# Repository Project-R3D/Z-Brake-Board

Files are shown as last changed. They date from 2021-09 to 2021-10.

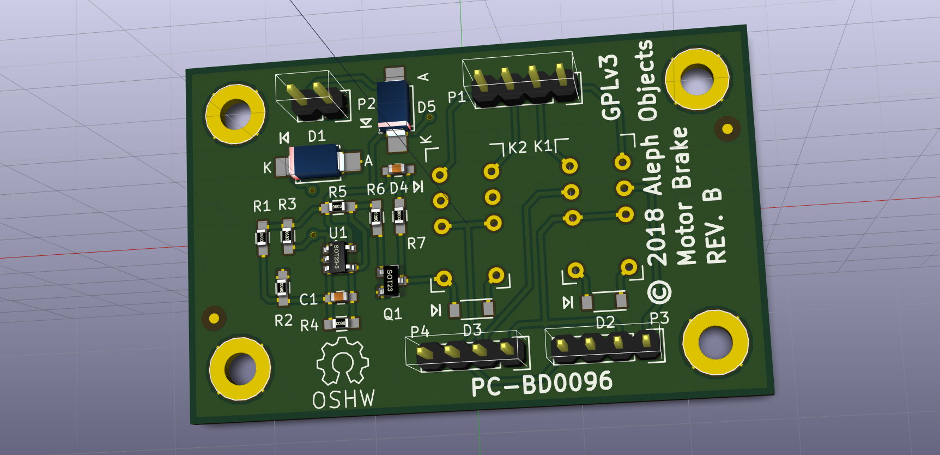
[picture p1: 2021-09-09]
Original_Lulz_Design/Z_Brake/Z_Brake.png

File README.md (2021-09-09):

# Lulzbot Z Motor Automatic Brake

The [original design files](/Original_Lulz_Design/) contained within this repository were backed up from http://devel.lulzbot.com/electronics/dolores/ on Sept 8, 2021.
In case that gets taken down as well, please see this [archive.org](https://web.archive.org/web/20200216141835/http://devel.lulzbot.com/electronics/dolores/) backup as well.

This repository acts as a backup to that original design (which was sadly removed from all other Lulzbot servers) while complying with the original `CC BY SA 4.0` AND `GPL v3` license.

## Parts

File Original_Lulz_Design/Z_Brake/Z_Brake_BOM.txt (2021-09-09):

Z_BRAKE BILL OF MATERIALS (BOM)

REFERENCE	DESCRIPTION					MFR. PART NUMBER	MFR.				NOTE

C1		Capacitor SMT 0603 Ceramic 0.22uF 50V X7R	CL10B224KB8VPNC		Samsung Electro-Mechanics
D1		Zener Diode SMA SMT 10.0V 1W +/- 5%		SMAZ10-13-F		Diodes Incorporated
D2		Schottky Diode SMT SOD-123 40V 300mA		BAT54ZFILM		STMicroelectronics
D3		Schottky Diode SMT SOD-123 40V 300mA		BAT54ZFILM		STMicroelectronics
D4		LED SMT 0603 Yellow Clear                       LTST-C190YKT		Lite-On Inc.
K1		Relay DIP 24V 2A DPDT				EC2-24NU		Kemet
K2		Relay DIP 24V 2A DPDT				EC2-24NU		Kemet
P1		Connector SL Header 4-Pin 1x4 0.100 Shrouded	0705430003		Molex, LLC
P2		Connector SL Header 2-Pin 1x2 0.100 Shrouded	0705430001		Molex, LLC
P3		Connector SL Header 4-Pin 1x4 0.100 Shrouded	0705430003		Molex, LLC
P4		Connector SL Header 4-Pin 1x4 0.100 Shrouded	0705430003		Molex, LLC
Q1		Transistor FET N-Channel SMT SOT-23 60V		2N7002			Central Semiconductor Corp	Vgs must be 30VDC minimum
R1		Resistor SMT 0603 12.4 k 1%			RC0603FR-0712K4L	Yageo
R2		Resistor SMT 0603 10.0 k 1%			RC0603FR-0710KL		Yageo
R3		Resistor SMT 0603 10.0 k 1%			RC0603FR-0710KL		Yageo
R4		Resistor SMT 0603 180 k 1%			RC0603FR-07180KL	Yageo
R5		Resistor SMT 0603 10.0 k 1%			RC0603FR-0710KL		Yageo
R6		Resistor SMT 0603 3.30 k 1%			RC0603FR-073K3L		Yageo
U1		IC SMT SOT-23-5 LM397				LM397MF/NOPB		Texas Instruments

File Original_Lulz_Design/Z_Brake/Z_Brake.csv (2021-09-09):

Id | Designator | Package | Quantity | Designation | Supplier and ref
1 | K1,K2 | EC2_Relay | 2 | EC2-24NU
2 | C1 | C_0603_HandSoldering | 1 | 0.22uF
3 | D1 | SMA_Handsoldering | 1 | 10.0 V ZENER
4 | D2,D3 | SOD-123 | 2 | D_Schottky_ALT
5 | D4 | C_0603_HandSoldering | 1 | LED_ALT
6 | Q1 | SOT-23 | 1 | 2N7002
7 | R1 | R_0603_HandSoldering | 1 | 12.6k
8 | R2,R3,R5,R6 | R_0603_HandSoldering | 4 | 10k
9 | R4 | R_0603_HandSoldering | 1 | 100k
10 | R7 | R_0603_HandSoldering | 1 | 3.3k
11 | U1 | SOT-23-5 | 1 | LM397
12 | P1,P3,P4 | Pin_Header_Straight_1x04 | 3 | CONN_01X04
13 | P2 | Pin_Header_Straight_1x02 | 1 | CONN_01X02
14 | MH1,MH2,MH3,MH4 | MOUNT_HOLE | 4 | CONN_01X01
15 | REF** | Symbol_OSHW-Logo_SilkScreen | 1 | Symbol_OSHW-Logo_SilkScreen
16 | D5 | SMA_Handsoldering | 1 | D_ALT

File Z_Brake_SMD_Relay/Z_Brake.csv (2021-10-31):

Comment | Designator | Footprint | LCSC
0.22uF | C1 | Capacitor_SMD:C_0603_1608Metric_Pad1.08x0.95mm_HandSolder
10.0 V ZENER | D1 | Diode_SMD:D_SMA_Handsoldering
D_Schottky_ALT | D2,D3 | Diode_SMD:D_SOD-123
LED | D4 | LED_SMD:LED_0603_1608Metric_Pad1.05x0.95mm_HandSolder
D_ALT | D5 | Diode_SMD:D_SMA_Handsoldering
EC2-24NU | K1,K2 | Relay_SMD:Relay_DPDT_Kemet_EE2_NU
CONN_01X01 | MH1,MH2,MH3,MH4 | MountingHole:MountingHole_2.5mm_Pad
CONN_01X04 | P1,P3 | Molex:Molex-70543-0038-0-0-MFG
CONN_01X02 | P2 | Molex:MOLEX_0705430001
2N7002 | Q1 | Package_TO_SOT_SMD:SOT-23_Handsoldering
12.4k | R1 | Resistor_SMD:R_0603_1608Metric_Pad0.98x0.95mm_HandSolder
180k | R4 | Resistor_SMD:R_0603_1608Metric_Pad0.98x0.95mm_HandSolder
10k | R2,R3,R5,R6 | Resistor_SMD:R_0603_1608Metric_Pad0.98x0.95mm_HandSolder
3.3k | R7 | Resistor_SMD:R_0603_1608Metric_Pad0.98x0.95mm_HandSolder
M2012C390 | RV1,RV2 | Resistor_SMD:R_0805_2012Metric_Pad1.20x1.40mm_HandSolder
LM397 | U1 | Package_TO_SOT_SMD:SOT-23-5_HandSoldering

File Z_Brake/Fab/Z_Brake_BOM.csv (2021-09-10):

Qty | Reference(s) | MPN | Manufacturer | Primary Supplier | Supplier PN
1 | C1 | CL10B224KB8VPNC | Samsung | Digikey | 1276-6600-1-ND
1 | D1 | SMAZ10-13-F | Diodes Incorporated | Digikey | SMAZ10-FDICT-ND
2 | D2, D3 | BAT48ZFILM | STMicroelectronics | Digikey | 497-5712-1-ND
1 | D4 | LTST-C190YKT | Lite-On Inc. | Digikey | 160-1184-1-ND
1 | D5 | CDBA340-HF | Comchip Technology | Digikey | 641-1748-1-ND
2 | K1, K2 | EC2-24NU | Kemet | Digikey | 399-11037-5-ND
2 | P1, P3 | 705430003 | Molex | Digikey | WM4802-ND
1 | P2 | 705430001 | Molex | Digikey | WM4800-ND
1 | Q1 | 2N7002 TR PBFREE | Central Semiconductor Corp | Digikey | 1514-2N7002TRPBFREECT-ND
1 | R1 | RC0603FR-0712K4L | YAGEO | Digikey | 311-12.4KHRCT-ND
4 | R2, R3, R5, R6 | RC0603FR-0710KL | YAGEO | Digikey | 311-10.0KHRCT-ND
1 | R4 | RC0603FR-07180KL | YAGEO | Digikey | 311-180KHRCT-ND
1 | R7 | RC0603FR-073K3L | YAGEO | Digikey | 311-3.30KHRCT-ND
2 | RV1, RV2 | AVR-M2012C390KT6AB | TDK | Digikey | 445-2549-1-ND
1 | U1 | LM397MF/NOPB | TI | Digikey | LM397MF/NOPBCT-ND

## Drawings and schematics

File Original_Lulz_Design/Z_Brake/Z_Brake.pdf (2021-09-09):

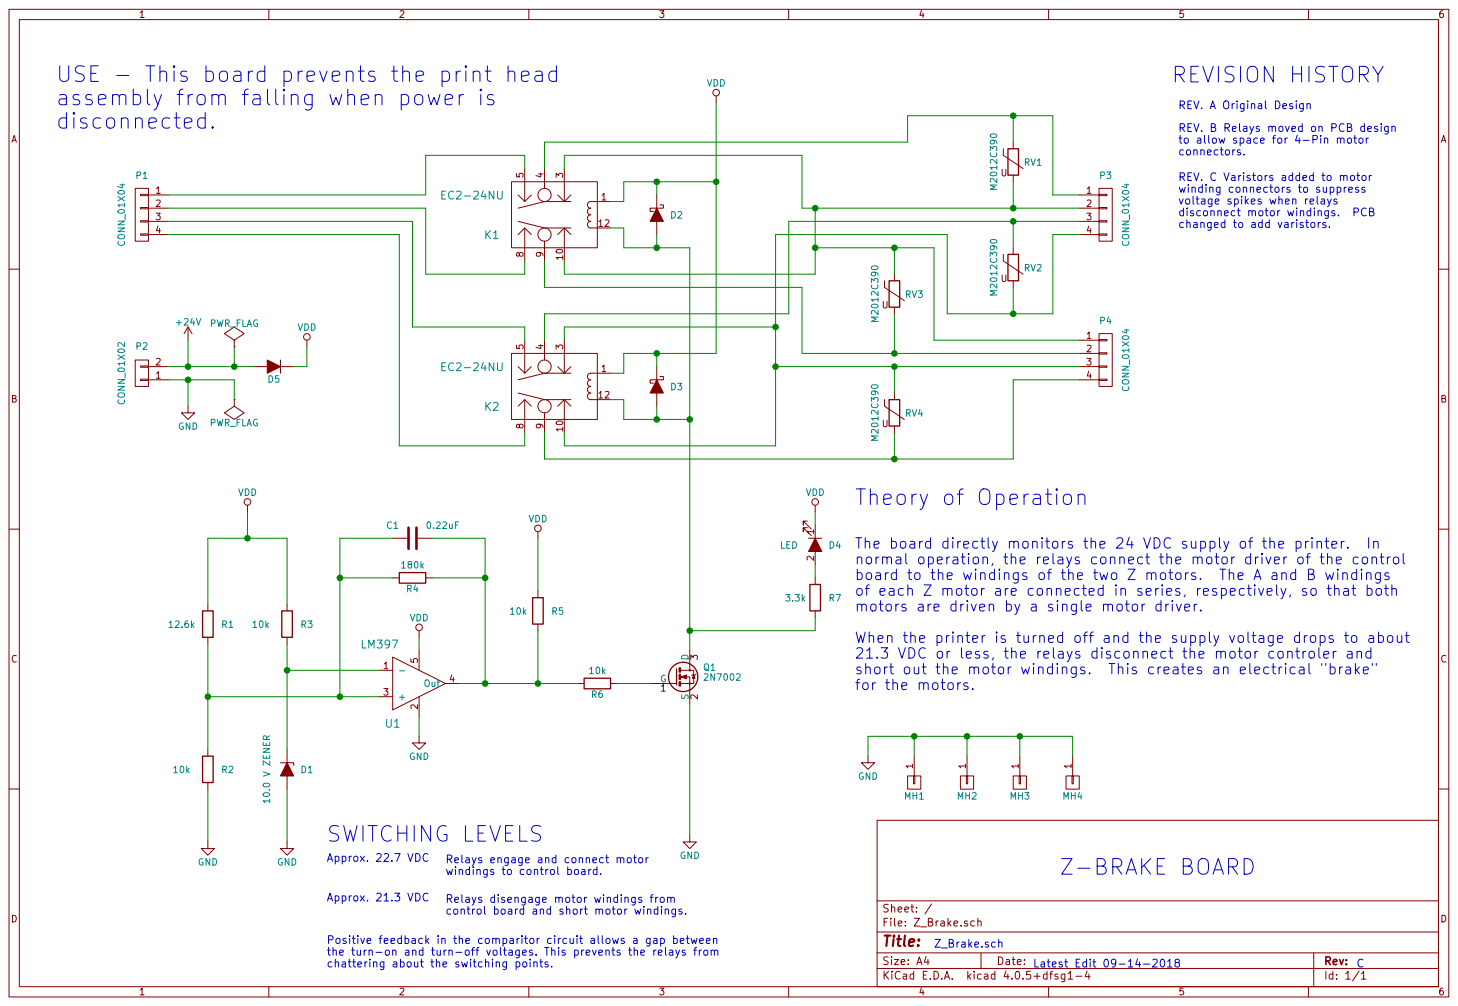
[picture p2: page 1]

USE - This board prevents the print head
assembly from falling when power is
disconnected.

REV. A Original Design
REV. B Relays moved on PCB design
to allow space for 4-Pin motor connectors. REV. C Varistors added to motor winding connectors to suppress

voltage spikes when relays
changed to add varistors.

The board directly monitors the 24 VDC supply of the printer. In
normal operation, the relays connect the motor driver of the control
board to the windings of the two Z motors. The A and B windings
of each Z motor are connected in series, respectively, so that both
motors are driven by a single motor driver.
When the printer is turned off and the supply voltage drops to about
21.3 VDC or less, the relays disconnect the motor controler and
short out the motor windings. This creates an electrical "brake"
for the motors.

Relays engage and connect motor
windings to control board.

Relays disengage motor windings from
control board and short motor windings.

Positive feedback in the comparitor circuit allows a gap between
the turn-on and turn-off voltages. This prevents the relays from
chattering about the switching points.

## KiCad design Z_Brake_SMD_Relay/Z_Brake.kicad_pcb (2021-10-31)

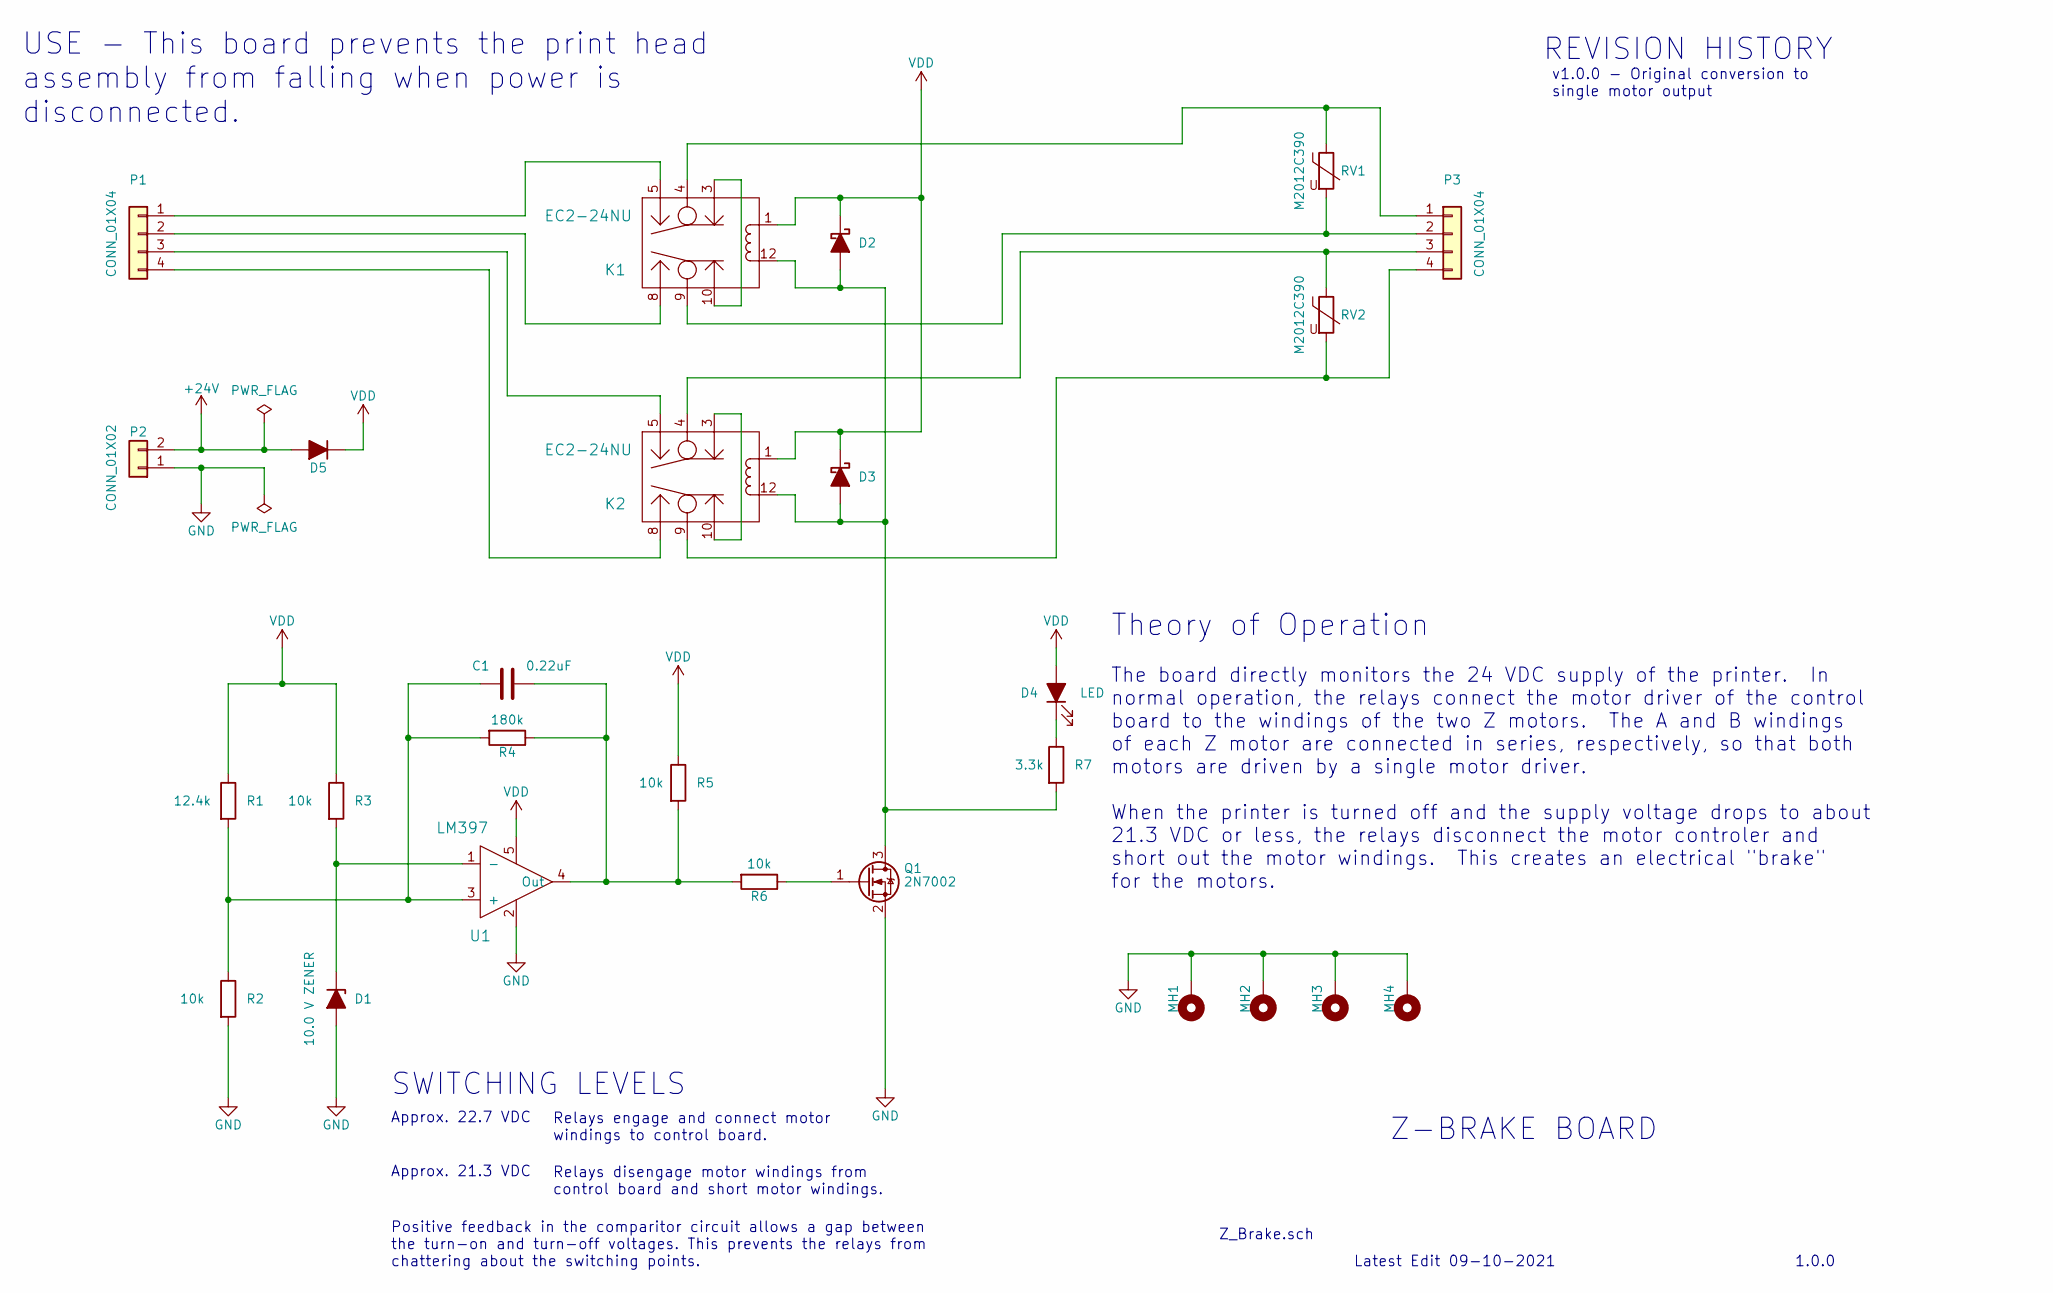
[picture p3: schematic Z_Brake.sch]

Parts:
C1: 0.22uF; C_0603_1608Metric_Pad1.08x0.95mm_HandSolder; MPN CL10B224KB8VPNC
D1: 10.0 V ZENER; D_SMA_Handsoldering; MPN SMAZ10-13-F
D2, D3: D_Schottky_ALT; D_SOD-123; MPN BAT48ZFILM
D4: LED; LED_0603_1608Metric_Pad1.05x0.95mm_HandSolder; MPN LTST-C190YKT
D5: D_ALT; D_SMA_Handsoldering; MPN CDBA340-HF
K1, K2: EC2-24NU; Relay_DPDT_Kemet_EE2_NU; MPN EC2-24NU
MH1, MH2, MH3, MH4: CONN_01X01; MountingHole_2.5mm_Pad
P1, P3: CONN_01X04; Molex-70543-0038-0-0-MFG; MPN 0705430003
P2: CONN_01X02; MOLEX_0705430001; MPN 0705430001
Q1: 2N7002; SOT-23_Handsoldering; MPN 2N7002 TR PBFREE
R1: 12.4k; R_0603_1608Metric_Pad0.98x0.95mm_HandSolder; MPN RC0603FR-0712K4L
R2, R3, R5, R6: 10k; R_0603_1608Metric_Pad0.98x0.95mm_HandSolder; MPN RC0603FR-0710KL
R4: 180k; R_0603_1608Metric_Pad0.98x0.95mm_HandSolder; MPN RC0603FR-07180KL
R7: 3.3k; R_0603_1608Metric_Pad0.98x0.95mm_HandSolder; MPN RC0603FR-073K3L
RV1, RV2: M2012C390; R_0805_2012Metric_Pad1.20x1.40mm_HandSolder; MPN AVR-M2012C390KT6AB
U1: LM397; SOT-23-5_HandSoldering; MPN LM397MF/NOPB

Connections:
+24V: D5.2 (A), P2.2
GND: D1.2 (A), MH1.1, MH2.1, MH3.1, MH4.1, P2.1, Q1.2 (S), R2.2, U1.2
unnamed: C1.1, R4.1, R5.2, R6.2, U1.4 (Out)
unnamed: C1.2, R1.2, R2.1, R4.2, U1.3 (+)
unnamed: D1.1 (K), R3.2, U1.1 (-)
unnamed: D2.2 (A), D3.2 (A), K1.12, K2.12, Q1.3 (D), R7.2
unnamed: D4.1 (K), R7.1
unnamed: K1.4, P3.1, RV1.1
unnamed: K1.5, P1.1
unnamed: K1.8, P1.2
unnamed: K1.9, P3.2, RV1.2
unnamed: K1.3, K1.10
unnamed: K2.4, P3.3, RV2.1
unnamed: K2.5, P1.3
unnamed: K2.8, P1.4
unnamed: K2.9, P3.4, RV2.2
unnamed: K2.3, K2.10
unnamed: Q1.1 (G), R6.1
VDD: D2.1 (K), D3.1 (K), D4.2 (A), D5.1 (K), K1.1, K2.1, R1.1, R3.1, R5.1, U1.5

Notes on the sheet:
Z-BRAKE BOARD
Z_Brake.sch
Latest Edit 09-10-2021
REVISION HISTORY
Approx. 22.7 VDC
SWITCHING LEVELS
Approx. 21.3 VDC
Relays engage and connect motor windings to control board.
Relays disengage motor windings from control board and short motor windings.
Theory of Operation
The board directly monitors the 24 VDC supply of the printer. In normal operation, the relays connect the motor driver of the control board to the windings of the two Z motors. The A and B windings of each Z motor are connected in series, respectively, so that both motors are driven by a single mot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
Positive feedback in the comparitor circuit allows a gap between the turn-on and turn-off voltages. This prevents the relays from chattering about the switching points.
USE - This board prevents the print head assembly from falling when power is disconnected.
1.0.0
v1.0.0 - Original conversion to single motor output

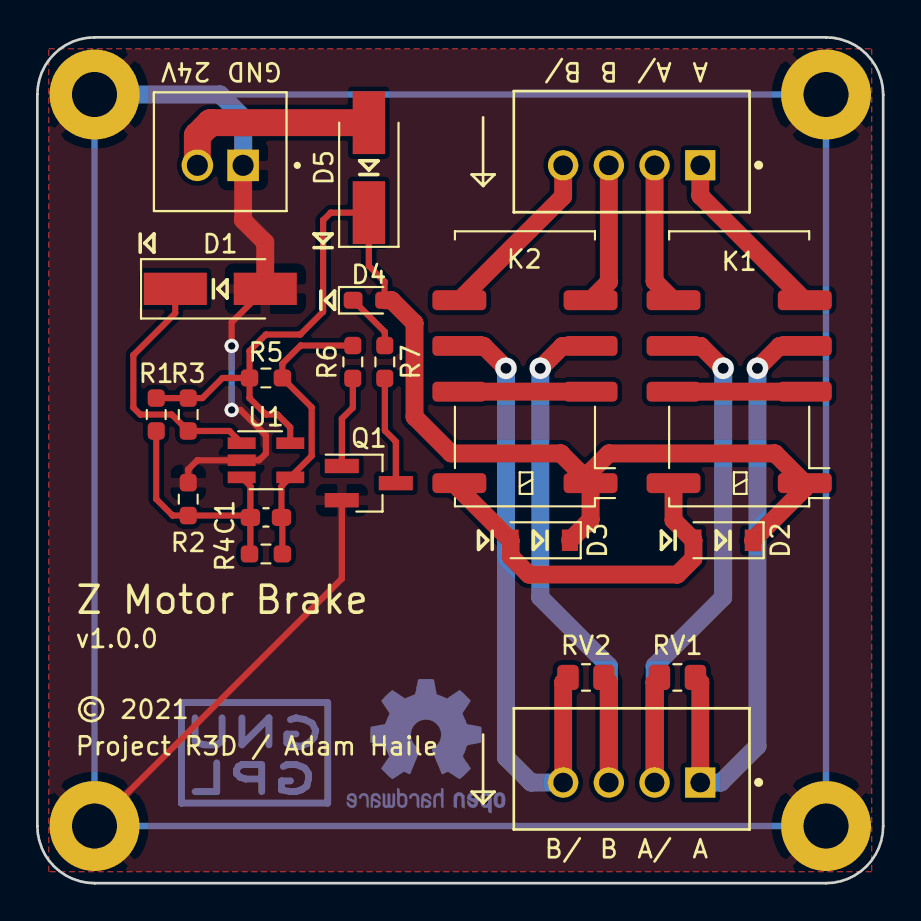
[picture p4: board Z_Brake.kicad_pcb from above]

Board: 2 copper layers, 47.0 x 47.0 mm, 26 parts (0 on the bottom side), 19 nets.

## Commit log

2021-09-09 Initial backup
    [Z_Brake.csv, Z_Brake.kicad_pcb, Z_Brake.sch]
2021-09-09 Start on conversion to new KiCAD
    [Z_Brake-2021-09-08-20-40-08.sch, Z_Brake.kicad_pcb, Z_Brake.sch]
2021-09-09 No more rescue files needed
    [Z_Brake-2021-09-08-20-40-08.sch]
2021-09-09 Converted to single motor output
    [Z_Brake.sch]
2021-09-09 Starting on PCB layout
    [Z_Brake.sch]
2021-09-10 Final PCB
    [Z_Brake.kicad_pcb, Z_Brake.sch]
2021-09-10 Add fab files
    [Z_Brake-B_Cu.gbr, Z_Brake-B_Mask.gbr, Z_Brake-B_SilkS.gbr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]
2021-10-07 JLCPCB pos file
    [Z_Brake-bottom-pos.csv, Z_Brake-top-pos.csv]
2021-10-31 Added smt relay version
    [Z_Brake-B_Cu.gbl, Z_Brake-B_Mask.gbs, Z_Brake-B_Paste.gbp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]

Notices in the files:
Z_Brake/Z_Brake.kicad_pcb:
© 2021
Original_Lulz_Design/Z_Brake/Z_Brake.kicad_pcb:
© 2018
